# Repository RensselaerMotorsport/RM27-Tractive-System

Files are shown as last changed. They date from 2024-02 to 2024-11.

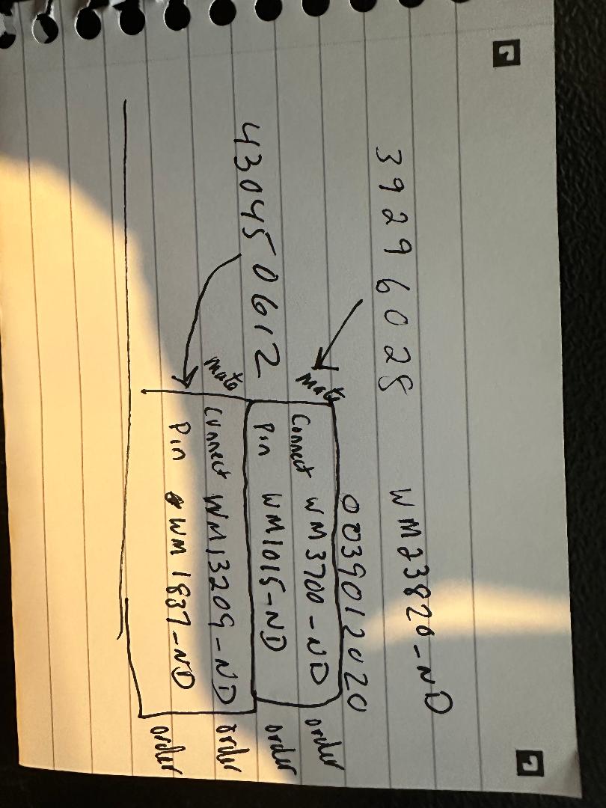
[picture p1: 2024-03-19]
mating connectors TSAL.jpg

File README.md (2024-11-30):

# RM27-TRACTIVE-SYSTEM

NOTICE!!!
This repo is OUTDATED! The current tractive system repository is at https://github.com/RensselaerMotorsport/RM28-Tractive-System
Almost all circuits from this repo were updated for the RM28 car (FSAE 2024 competition car)

This respository currently contains one major project:
* WIP RM27 Project - This project is the most up-to-date version of the 2023-2024 competition car's High Voltage System.

To open and work with these files, specific software packages must be used.
* LTSpice - Circuit simulation software used for preliminary mockups of circuit designs. The .asc files can be opened in other spice programs like ngspice or pspice, but these circuits were originally drafted in LTSpice
* KiCad - PCB design software used for creating schematics for manufacturing.

Acronyms Used:
* ESF - Elecrtrical Systems Form
* GLV - Grounded Low Voltage
* HV - High Voltage
* TSAL - Tractive System Active Light

Typical Circuits:
* Tractive System Active Light (TSAL) - When GLV is on and HV (typically between 12-400V) is less than 60V outside the container, turns an LED green. If HV is greater than 60V, a red LED blinks at low frequency. PS16-051 is the transformer used in this circuit, but has been since discontinued. A similar transformer may need to be selected.
* Accumulator Indicator - Turns on blue LED if voltage outside the container is greater than 60V. Must work in absence of GLV.
* ESF - Shows overall design of racecar electrical system. Includes datasheets, circuit diagrams, electrical architecture, and part numbers.

Additional Circuits in this repo:
The soldering demo board for the Mercer XLab was included to be used as an instructional tool to teach other students at RPI how to solder. Several PCBs were printed and the Rensselaer Motorsport club ran a soldering workshop in the XLab. The board is a simple multivibrator that uses a potentiometer to adjust the blinking frequency of an LED. This workshop was quite successful for our lab, however keep in mind if you run a workshop with this circuit, we designed this circuit to be used with a 3V button cell battery (CR2025). Make sure that a 555 timer designed to have a 3V power rail us used so the timer works sufficiently. (We used the TLC555CP).

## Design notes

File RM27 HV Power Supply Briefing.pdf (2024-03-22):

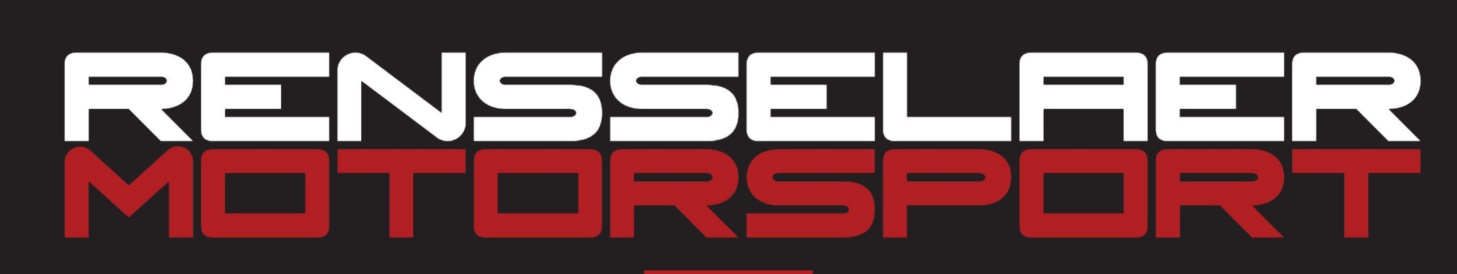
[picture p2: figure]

## RM27 HV Power Supply Briefing

Sean Trimper - ESO
trimps@rpi.edu - (603)204-0353 March, 2024

### - Use fancy HVPS without injury

## Goal

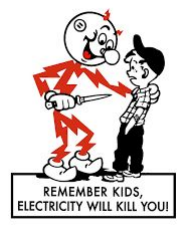
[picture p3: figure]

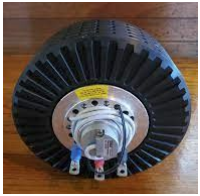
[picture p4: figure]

- In addition to being connected to 400V, the motor is heavy and

moving (and EXPENSIVE)

- The entire motor casing spins FAST
- Even if the motor has stopped moving:
- Ensure power is cut off from the tractive system
- Motor will be hot
- The ESC handles many volts and amps

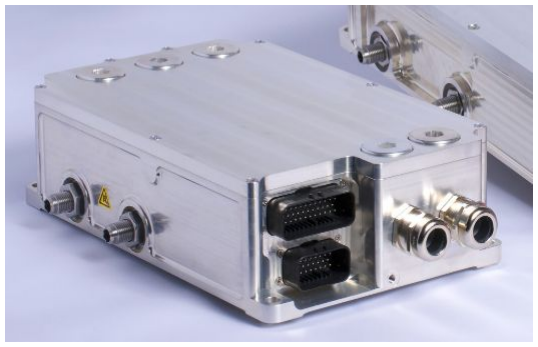
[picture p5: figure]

- ESC will be hot
- If handling motor or ESC, contact ESO

## Powertrain

## HVPS

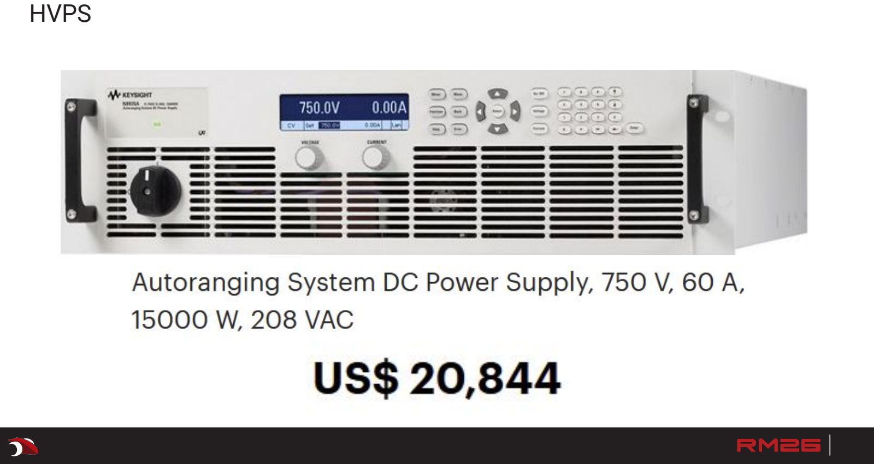
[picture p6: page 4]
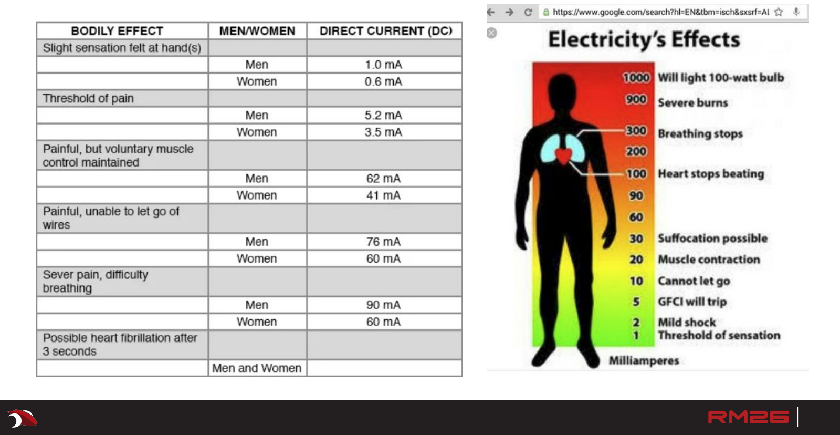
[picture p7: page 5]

- >50V = dead
- Do not touch the HVPS unless Sean tells you to
- Do not approach the setup when HVPS is on unless told to

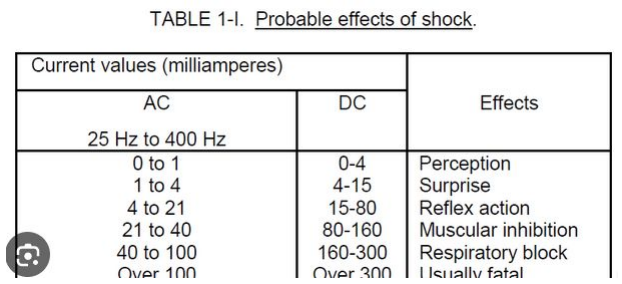
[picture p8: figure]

- Will announce verbally when HV work is being conducted and when it is over
- Treat the person with HV equipment on like they are actively welding
- If you touch it, you will have 1.5A (1500mA) across your heart at HV
- If you touch it, you will not be able to move, and will be “glued” to it (15mA)
- Electrical beating stick!
- Touch recently energized things with back of your hand (inverter, etc.)
- Keep one hand in your back pocket if not wearing HV gloves near HVPS

## High voltage

- Please familiarize yourself with the Shop Safety Manual
- Has EHS & faculty advisor approved guidelines on electrical work and safety
- If any questions arise while working, please ask in-person or on slack

## Questions?

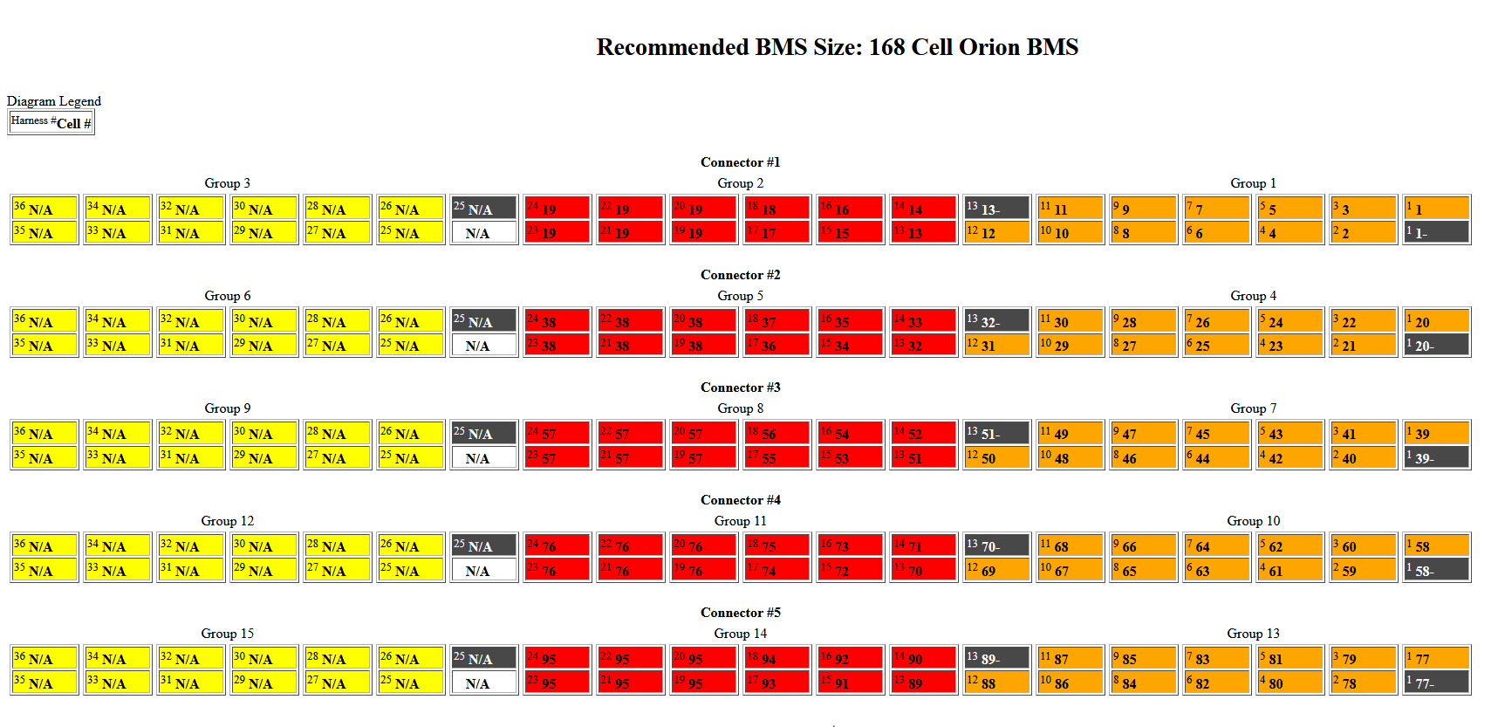
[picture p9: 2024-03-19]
BMS2-Voltage-Tap-Diagram.png

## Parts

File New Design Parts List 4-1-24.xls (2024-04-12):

Item | Qty | Reference | Part Description | Manufacturer / Part #
1 | 1 | C2 | CAP., 3.3uF, ALUM,450V,20% | NICHICON, ULT2W3R3MNL1GS | 493-6729-1-ND
2 | 1 | C3 | CAP., 10uF, X5R, 25V, 20%, 0603 | MURATA, GRM188R61E106MA73D | 490-7202-1-ND
3 | 1 | C8 | CAP., 10uF, X7R, 25V, 10%, 1206 | MURATA, GRM31CR71E106KA12L | 490-6518-1-ND
4 | 1 | C4 | CAP., 10pF, C0G, 630V,5%, 1206 | MURATA, GRM31A5C2J100JW01D | 490-11620-1-ND
5 | 1 | C5 | CAP., 0.33uF, X5R, 25V,10%, 0603 | AVX, 06033D334KAT2A | 478-KGM15BR51E334KTCT-ND
6 | 2 | C11,C12 | CAP., 22uF,X7R, 16V, 10%, 1210 | MURATA , GRM32ER71C226KE18L | 490-5313-1-ND
7 | 1 | C14 | CAP., 0.47uF, X7T, 450V, 10%, 1812 | TDK, C4532X7T2W474K230KA | 445-7771-1-ND
8 | 1 | C16 | CAP., 0.1uF, X7R, 25V, 10%, 0603 | MURATA, GRM188R71E104KA01D | 490-6051-1-ND
9 | 2 | D2,D3 | DIODE, RECTIFIER 600V, 1A, SOD123F | FAIRCHILD, ES1JFL | 1801-ES1JFLCT-ND
10 | 1 | D4 | DIODE SCHOTTKY, 30V, 200MA, SOD323 | CENTRAL SEMI., CMDSH2-3 TR | 1514-CMDSH2-3TRPBFREECT-ND
11 | 2 | D1, D5 | DIODE, ZENER, 5W,DO-214AA | MCC, SMBJ5350B-TP | SMBJ5350B-TPMSCT-ND
12 | 1 | N/A
13 | 1 | JP1 | Molex | 39296028 | WM23820-ND
14 | 1 | JP1 Mate | Molex | 39012025 | WM23700-ND
15 | 3 | JP1 Mate pin | Molex | 39000038 | WM2501CT-ND - Cut Tape (CT)
16 | 1 | JP2 | Molex | 532650229 | 0532650229-ND
17 | 1 | JP2 Mate | Molex | 510670200 | WM3330-ND
18 | 3 | JP2 Mate Pin | Molex | 502178000 | WM3316CT-ND
19 | 1 | L1 | INDUCTOR, 1500uH Wurth | 7447709152 | 732-4122-1-ND
20 | 1 | R3 | RES., CHIP, 4.99K, 1/4W, 1%, 1206 | VISHAY, CRCW12064K99FKEA | 541-4.99KFCT-ND
21 | 1 | R6 | RES., CHIP, 22.1k, 1/10W , 1%, 0603 | VISHAY, CRCW060322K1FKEA | 541-22.1KHCT-ND
22 | 1 | R9 | RES., CHIP, 10.7K, 1/10W, 1%, 0603 | VISHAY, CRCW060310K7FKEA | 541-10.7KHCT-ND
23 | 1 | R10 | RES., CHIP, 1.24K,1/10W, 1%, 0603 | VISHAY, CRCW06031K24FKEA | 541-1.24KHCT-ND
24 | 1 | R12 | RES., CHIP, 0.33 OHM, 0.2W, 1%, 0603 | RCWE0603R330FKEA | RCWE.33CCT-ND
25 | 1 | U1 | I.C., LT8315EFE | LINEAR, LT8315EFE#PBF | 505-LT8315EFE#PBF-ND
26 | 4 | MH1-MH4 | STANDOFF, NYLON, 0.25" | KEYSTONE, 8831 (SNAP ON) | 36-8831-ND
27 | 4 | R1,R2,R4,R5 | RES., CHIP, 249K, 1/4W, 1%, 1210 |  | 541-249KAACT-ND
28 | 1 | R7 | RES., CHIP, 20K, 1/4W, 1%, 1210 |  | 541-20.0KAACT-ND
29 | 1 | R8 | RES., CHIP, 1K, 1/4W, 1%, 1210 |  | 541-1.00KAACT-ND
30 | 2 | R100,R101 | RES., CHIP, 0, 1/10W, 1%, 0603 |  | 541-0.0GCT-ND
 |  |  | Bom changes on 8/3/17,9/5/17
5 | 1 | C5 | CAP., 0.33uF, X7R, 25V,10%, 0603 | TDK, C1608X7R1E334K080AC | 0 |  | 0 | Req,4/11/17
9 | 1 | D2 | DIODE, 600V, 1A, SOD123F | CENTRAL SEMI., CMMMR1U-06 TR | 0 | 500 | 500
9 | 1 | D3 | DIODE, SCHOTTKY 600V, 1.7A, 10PQFN | CREE, C3D1P7060Q | 0 |  | 0 |  | Lead Lime 18 weeks
18 | 1 | R9 | RES., CHIP, 5.36K, 1/10W, 1%, 0603 | VISHAY, CRCW06035K36FKEA | 0 |  | 0 | fr.1317A
19 | 1 | R10 | RES., CHIP, 619,1/10W, 1%, 0603 | VISHAY, CRCW0603619RFKEA | 0 | 2800 | 2800

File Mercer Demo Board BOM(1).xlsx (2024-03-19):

Part | Value | price/1 | link | Manufacturer P/N | Vendor Number | Vendor
U1 | 555 timer | 0.94 | https://www.digikey.com/en/products/detail/texas-instruments/TLC555CP/277502 | TLC555CP | 296-1857-5-ND | Digikey
J1 | N/A | 0.58 | https://www.amazon.com/LAMPVPATH-CR2032-Battery-Holder-Mounting/dp/B08SQJJJNK?s=electronics |  | B08SQJJJNK | Amazon
Button Cell | 3V | 0.4 | Button Cell (https://www.amazon.com/Powerowl-Capacity-Lithium-Battery-20-Pack/dp/B08ML4X69J?s=electronics) |  | B08ML4X69J
R2 | 1kohm | 0.1 | https://www.digikey.com/en/products/detail/stackpole-electronics-inc/CF14JT1K00/1741314 | CF14JT1K00 | CF14JT1K00CT-ND - Cut Tape (CT) | DIgikey
D1 | 1.9V | 0.28 | https://www.digikey.com/en/products/detail/sunled/XLUR12D/4745846 | XLUR12D | 1497-1031-ND | Digikey
Rpot |  | 1.2 | https://www.digikey.com/en/products/detail/tt-electronics-bi/P090S-14T20BR10K/2408854 | P090S-14T20BR10K | 987-1277-ND | Digikey
C1 | 10uF | 0.1 | https://www.digikey.com/en/products/detail/yageo/CC0805KRX7R9BB104/302874 | CC0805KRX7R9BB104 | 311-1140-1-ND - Cut Tape (CT) | Digikey
S1 | N/A | 1.5 | https://www.digikey.com/en/products/detail/cw-industries/GF-123-0054/4089770 | GF-123-0054 | CWI333-ND | Digikey
R1 | 150ohms | 0.1 | https://www.digikey.com/en/products/detail/stackpole-electronics-inc/RNF14FTD150R/1706642 | RNF14FTD150R | RNF14FTD150RCT-ND - Cut Tape (CT) | Digikey

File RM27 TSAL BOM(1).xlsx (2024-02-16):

Part | Value | Description | MFG Part Number | price/1 | price per accu | link | Total price | Vendor Number | Vendor
R6,R7,R4,R2 | 249kohm | R_1206_3216Metric_Pad1.42x1.75mm_HandSolder | RCV1206249KFKEA | 0.3 | 1.2 | https://www.mouser.com/ProductDetail/Vishay-Draloric/RCV1206249KFKEA?qs=hWgE7mdIu5TjDQ%252B0bO60Fg%3D%3D | 22.02 | 71-RCV1206249KFKEA | Mouser
J2 | Connector | Molex_Mini-Fit_Jr_5566-02A_2x01_P4.20mm_Vertical | 39296028 | 1.28 | 1.28 | https://www.digikey.com/en/products/detail/molex/0039296028/930308 |  | WM23820-ND | Digikey
R10, R11 | 100ohm | R_1206_3216Metric_Pad1.42x1.75mm_HandSolder | CRCW1206100RFKEAHP | 0.23 | 0.46 | https://www.digikey.com/en/products/detail/vishay-dale/CRCW1206100RFKEAHP/2222416 |  | 541-100UCT-ND - Cut Tape (CT) | Digikey
R12 | 1Mohm | R_1206_3216Metric_Pad1.42x1.75mm_HandSolder | CRCW12061M00FKEAC | 0.1 | 0.1 | https://www.digikey.com/en/products/detail/vishay-dale/CRCW12061M00FKEAC/7928596 |  | 541-4174-1-ND - Cut Tape (CT) | Digikey
C3,C4,C5 | 100nF | C_0805_2012Metric_Pad1.15x1.40mm_HandSolder | C0805C104K4RAC7800 | 0.19 | 0.57 | https://www.digikey.com/en/products/detail/kemet/C0805C104K4RAC7800/411166 |  | 399-C0805C104K4RAC7800CT-ND - Cut Tape (CT | Digikey
C2 | 10nF | C_0805_2012Metric_Pad1.15x1.40mm_HandSolder | C0805C104K4RAC7800 | 0.13 | 0.13 | https://www.digikey.com/en/products/detail/kemet/C0805C103K3RAC7800/2209705 |  | 399-C0805C103K3RAC7800CT-ND - Cut Tape (CT) | Digikey
R5 | 900ohm | R_1206_3216Metric_Pad1.42x1.75mm_HandSolder | RT1206CRE07900RL | 0.23 | 0.23 | https://www.digikey.com/en/products/detail/yageo/RT1206CRE07900RL/5938251 |  | 13-RT1206CRE07900RLCT-ND - Cut Tape (CT) | Digikey
R8 | 49k9 | R_1206_3216Metric_Pad1.42x1.75mm_HandSolder | ERJ-P08D4992V | 0.28 | 0.28 | https://www.digikey.com/en/products/detail/panasonic-electronic-components/ERJ-P08D4992V/9812440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 |  | 10-ERJ-P08D4992VCT-ND - Cut Tape (CT | Digikey
R9,R19,R13 | 2k2 | R_1206_3216Metric_Pad1.42x1.75mm_HandSolder | ERJ-P08F2201V | 0.21 | 0.63 | https://www.digikey.com/en/products/detail/panasonic-electronic-components/erj-p08f2201v/9812790 |  | 10-ERJ-P08F2201VCT-ND - Cut Tape (CT) | Digikey
D2 | 12V | D_DO-35_SOD27_P7.62mm_Horizontal | 1N5242BTR | 0.16 | 0.16 | https://www.digikey.com/en/products/detail/onsemi/1N5242BTR/977598 |  | 1N5242BFSCT-ND - Cut Tape (CT) | Digikey
R3 | 24kohm | R_1206_3216Metric_Pad1.42x1.75mm_HandSolder | CRCW120624K0FKEAC | 0.1 | 0.1 | https://www.digikey.com/en/products/detail/vishay-dale/CRCW120624K0FKEAC/7920772 |  | 541-CRCW120624K0FKEACCT-ND - Cut Tape (CT) | Digikey
Q3,Q1 | 2N7002 | SOT-23 | 2N7002 | 0.45 | 0.9 | https://www.digikey.com/en/products/detail/onsemi/2N7002/244345 |  | 2N7002NCT-ND - Cut Tape (CT) | Digikey
R18,R14 | 10k | R_1206_3216Metric_Pad1.42x1.75mm_HandSolder | CRCW120610K0FKEBC | 0.1 | 0.2 | https://www.digikey.com/en/products/detail/vishay-dale/CRCW120610K0FKEBC/7921127 |  | 541-CRCW120610K0FKEBCCT-ND - Cut Tape (CT) | Digikey
D1 | D | D_SMA | US1MDFQ-13 | 0.44 | 0.44 | https://www.digikey.com/en/products/detail/diodes-incorporated/US1MDFQ-13/6187532 |  | US1MDFQ-13DICT-ND - Cut Tape (CT) | Digikey
Q4,Q2 | MCT06P10-TP | SOT-223-3_TabPin2 | MCT06P10-TP | 0.77 | 1.54 | https://www.digikey.com/en/products/detail/micro-commercial-co/MCT06P10-TP/10054657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 |  | MCT06P10-TPMSCT-ND - Cut Tape (CT) | Digikey
J1 | Connector | Molex_Micro-Fit_3.0_43045-0612_2x03_P3.00mm_Vertical | 430450612 | 1.52 | 1.52 | https://www.digikey.com/en/products/detail/molex/0430450612/252504?s=N4IgTCBcDaICwGYAMcCsBaJA2AjBAugL5A |  | WM1791-ND | Digikey
U2 | LM311 | SOIC-8_3.9x4.9mm_P1.27mm | LM311DR | 0.42 | 0.42 | https://www.digikey.com/en/products/detail/texas-instruments/LM311DR/381217 |  | 296-1388-1-ND - Cut Tape (CT) | Digikey
R17 | 220kohm | R_1206_3216Metric_Pad1.42x1.75mm_HandSolder | CRCW1206220KFKEAHP | 0.23 | 0.23 | https://www.digikey.com/en/products/detail/vishay-dale/CRCW1206220KFKEAHP/2228003 |  | 541-220KUCT-ND - Cut Tape (CT) | Digikey
R15,R16 | 22kohm | R_1206_3216Metric_Pad1.42x1.75mm_HandSolder | CRCW120622K0FKEA | 0.1 | 0.2 | https://www.digikey.com/en/products/detail/vishay-dale/CRCW120622K0FKEA/1176794 |  | 541-22.0KFCT-ND - Cut Tape (CT) | Digikey
U4 | NE555 | SOIC-8_3.9x4.9mm_P1.27mm | NE555DR | 0.47 | 0.47 | https://www.digikey.com/en/products/detail/texas-instruments/NE555DR/372491 |  | 296-6501-1-ND - Cut Tape (CT) | Digikey
U3 | 4N35 | DIP-6_W7.62mm | 4N35 | 0.74 | 0.74 | https://www.digikey.com/en/products/detail/vishay-semiconductor-opto-division/4N35/1738522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 |  | 4N35-ND | Digikey
C6,C1 | 1uF | C_0805_2012Metric_Pad1.15x1.40mm_HandSolde | C0805C105K4RACAUTO | 0.17 | 0.34 | https://www.digikey.com/en/products/detail/kemet/C0805C105K4RACAUTO/3314924 |  | 399-6930-1-ND - Cut Tape (CT) | Digikey
D3 | VHI | LED_0805_2012Metric_Pad1.15x1.40mm_HandSolder | CMD17-21VRD/TR8 | 0.76 | 0.76 | https://www.digikey.com/en/products/detail/visual-communications-company-vcc/CMD17-21VRD-TR8/254853 |  | L62501CT-ND - Cut Tape (CT) | Digikey
U1 | SPAN02A-12 | SPAN02 | SPAN02A-12 | 8.74 | 8.74 | https://www.mouser.com/ProductDetail/MEAN-WELL/SPAN02A-12?qs=5aG0NVq1C4wxQqKsG84AkQ%3D%3D |  | 709-SPAN02A-12 | Mouser
R1 | 75kohm | R_1206_3216Metric_Pad1.42x1.75mm_HandSolder | CRCW120675K0FKEAHP | 0.38 | 0.38 | https://www.digikey.com/en/products/detail/vishay-dale/CRCW120675K0FKEAHP/2227954 |  | 541-CRCW120675K0FKEAHPCT-ND - Cut Tape (CT) | Digikey

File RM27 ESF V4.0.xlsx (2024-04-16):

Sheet: Overview
Instructions |  |  | Status
-All cells for input have an orange background. -Cells, sections and worksheets have an overall status. The status cells have a blue background. -For sections which require an image or schematic, the image should be pasted and located over the specified area. Images should be pasted at a high resolution and then resized. This allows the reader to zoom into the image if more resolution is required. -Where datasheets are requested, a hyperlink to the datasheet from the manufacturer must be provided. -Additional Comments sections are provided throughout for documentation of things which the team feels are not adequately documented in the provided fields. These are optional and do not need to be completed. |  |  | Datasheets | OK
 |  |  | TS Schematics | OK
 |  |  | Accumulator | OK
 |  |  | Precharge/Discharge | OK
 |  |  | Charging | OK
 |  |  | Shutdown Circuit | OK
 |  |  | Torque Security | OK
 |  |  | Other | OK
 |  |  | Team Name | Rensselaer Motorsport
 |  |  | University | Rensselaer Polytechnic Institute
 |  |  | Competition Year | 2024
 |  |  | Max TS Voltage | 399 | V
 |  |  | Accumulator Fuse | 90 | A
Additional Comments
Template Revision History
Version | Date | Comment
2.3 | 2023-10-29 | Updated for 2024 season.
2.2 | 2022-11-03 | Updated for 2023 season.
2.1 | 2021-10-22 | Updated for 2022 season.
2.0 | 2020-11-27 | Multiple updates and bug fixes.

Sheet: Datasheets
Status | OK
Battery Cell |  |  |  | OK
Make |  | Molicel
Model |  | P28A
Nominal Capacity |  | 2.8 | Ahr
Maximum Voltage |  | 4.2 | V
Nominal Voltage |  | 3.6 | V
Minimum Voltage |  | 2.5 | V
Max output current |  | 35 | A
Max continuous current |  | 25 | A
Max Cell temp |  | 60 | C
Cell Chemistry |  | LiNiMnCoO2 (NMC)
Datasheet |  | https://www.molicel.com/wp-content/uploads/INR18650P28A-V1-80093.pdf
SDS |  | https://www.molicel.com/wp-content/uploads/00058ar-Molicel-SDS-Y2020.pdf
Additional Comments
Conductors |  |  |  |  |  |  |  |  | OK
Manufacturer | Part Number | Size [mm2] | Voltage [V] | Ampacity [A] | Max Temp [C] | Datasheet |  | Location Used |  | Additional Comments |  |  |  |  | Rules References
Champlain Cable EXRAD | EXRAD® ERGOFLEX ISO 19642-9 EXRAD–EF/EF-TW-50 | 50 | 1000 | 160 | 150 | https://www.champcable.com/wp-content/uploads/2021/06/219.-EXRAD-ERGOFLEX-Shielded-Thin-Wall-Battery-Cable-R3.pdf |  | Internal accumulator components, inverter to motor | OK | Listed Ampacity is at maximum allowed conductor temperature of 150C. At 90C, it is 260 Amps. Shielded |  |  |  |  | EV.5.2.1 EV.5.2.5 EV.6.3 EV.6.3.2 EV.6.6.4
Team Built | Busbar Collector | 79.6 | N/A | 154 | 90 | N/A |  | Accumulator Segment Poles | OK | Copper collectors
Team Built | Busbar | 2.5 | N/A | 9.7 | 90 | N/A |  | Accumulator segments (negative side of cells) | OK | Parallel nickel bus bars
Super Vu-Tron | 01764 | 55 | 600 | 260 | 90 | https://www.awcwire.com/product/01764 |  | Accumulator to inverter (including energy meter, HVD) | OK | Additional high current wire (unshielded)
AWC | M22759/22-22 | 0.34 | 600 | 0.92 | 200 | https://www.awcwire.com/product/m22759_22-22 |  | IMD, Precharge, Discharge | OK | HV to IMD and pre/discharge wiring
KOLACEN | ‎KLFH-027 | 1.31 | 250 | 15 | N/A | https://www.ubuy.com.bh/en/product/40R2G2HDU-kolacen-automotive-car-inline-screw-type-6x30mm-agc-fuse-holder-16-awg-wire-pcak-of-10 |  | AMS Fuse Holder | OK | Fuse holder from voltage tap to BMS
Fuses |  |  |  |  |  |  |  |  | OK
Manufacturer | Part Number | Voltage [V] | AC/DC | Current [A] | Interrupt [A] | Datasheet |  | Location Used |  | Additional Comments |  |  |  |  | Rules References
Bojack | F2AL250V | 250 | DC | 2 | 1000 | AMS Fuse (https://www.amazon.com/BOJACK-5x20mm-F2AL250V-Fast-Blow-Glass/dp/B07S768TPM) |  | AMS voltage sense | OK |  |  |  |  |  | EV.5.2.1 EV.6.6
Littelfuse | L50QS090.T | 500 | DC | 90 | 50000 | Main Fuse (https://www.mouser.com/datasheet/2/240/L50QS_High_Speed_Fuse_Datasheet-3311429.pdf) |  | Main Fuse | OK
Bel Fuse | 0ADKC5000-BE | 500 | DC | 5 | 20000 | Energy Meter Fuse (https://www.mouser.com/datasheet/2/643/ds_cp_0adkx_series-1960352.pdf) |  | Energy Meter Fuse | OK
Schurter Inc. | 8020.5071.G | 400 | DC | 2 | 1500 | IMD Fuse (https://www.schurter.com/en/datasheet/typ_SHF_6.3x32.pdf) |  | IMD | OK | HV to IMD (needed due to wires >= 150mm)
Resistors |  |  |  |  |  |  |  |  |  |  |  | OK
Manufacturer | Part Number | Voltage [V] | Resistance [Ω] | Power [W] | Power for 15 sec [W] | Heatsink [°C/W] (Enter "None" if no heatsink) |  |  | Datasheet |  | Location Used |  | Additional Comments |  |  |  | Rules References
Caddock Electronics Inc. | MP925-10.0K-1% | 500 | 10,000 | 25 | N/A | None |  |  | MP925 (https://www.mouser.com/datasheet/2/62/MP9000_Series-1052.pdf) |  | TSMP | OK |  |  |  |  | EV.5.2.1 EV.5.6 EV.5.8.4
Ohmite | 850F750E | 1170 | 750 | 50 | 750 | 3 |  |  | 850F750E (https://www.ohmite.com/assets/docs/res_89.pdf?r=false) |  | Precharge/Discharge | OK | Manufacturer tests at 5x rated power for 5sec. 250W>212W peak. 50W>46W avg.
Contactors/Relays |  |  |  |  |  |  |  |  | OK
Manufacturer | Part Number | Voltage [V] | Continuous Current [A] | Max Interrupt Current [A] | Normal State | Datasheet |  | Location Used |  | Additional Comments |  |  |  |  | Rules References
TE Connectivity / Kilovac | LEV200A4NAA | 900 | 500 | 2000 | NO | LEV200A4NAA (https://www.mouser.com/datasheet/2/418/ENG_CS_5-1773450-5_sec7_LEV200_0313_5-1773450-5_Se-1074401.pdf) |  | AIR | OK |  |  |  |  |  | EV.5.2.1 EV.5.4 EV.5.6
Cynergy3 | DBT71205F-HR | 3500 | 3 | 2 | NC | DBT71205F-HR (https://www.mouser.com/datasheet/2/657/cynergy3_d_hr_v2-1892317.pdf) |  | Discharge | OK
Cynergy3 | DAT71205F-HR | 3500 | 3 | 2 | NO | DAT71205F-HR (https://www.mouser.com/datasheet/2/657/cynergy3_d_hr_v2-1892317.pdf) |  | Precharge | OK
Connectors |  |  |  |  |  |  |  | OK
Manufacturer | Part Number | Voltage [V] | Ampacity [A] | Wire Size [mm2] | Datasheet |  | Location Used |  | Additional Comments |  |  |  |  | Rules References
Amphenol | MSDM5002 | 1000 | 500 | 50 | HVD Plug (https://www.mouser.com/datasheet/2/18/1/msd_m_xxxx_rev_a_cdr-1853453.pdf) |  | HVD | OK | HVD, Plug |  |  |  |  | EV.5.2.1 EV.5.10 EV.6.3.3
Amphenol | MSDF000R | 1000 | 500 | 50 | HVD Receptacle (https://www.mouser.com/datasheet/2/18/Amphenol_08092019_MSDF000R-1626989.pdf) |  | HVD | OK | HVD, Receptacle. HVD is main conductor connector for current to controller
Amphenol | RL0-080-1-50 | 1000 | 200 | 50 | RLO-080-1-50 (https://www.mouser.com/datasheet/2/18/1/IDS_67_RADLOK-372465.pdf) |  | Accumulator Segments | OK | Maintenance Plug, Connector
Amphenol | RL9080-101 | 1000 | 200 | 50 | RL9080-101 (https://www.mouser.com/datasheet/2/18/1/IDS_67_RADLOK-372465.pdf) |  | Accumulator Segments | OK | Maintenance Plug, Pin
Littelfuse | 576-03450613H | 600 | 20 | N/A | E-Meter Fuse Holder (https://www.mouser.com/datasheet/2/240/media-3319810.pdf) |  | Energy meter fuse holder | OK | Soldered terminals, low current fuse
Amphenol | PL28V-301-50 | 1000 | 300 | 70 | Exit Plug (https://www.mouser.com/datasheet/2/18/1/c_powerlok_right_angle_plugs_1_2_3_way_cdr-1701769.pdf) |  | Outer wall of accumulator container, charger output to accumulator | OK | Exterior Container Plug
Amphenol | PL00V-301-10M8 | 1000 | 300 | 70 | Exit Pin (https://www.amphenol-industrial.de/media/pages/produkte/ev-steckverbinder/powerlok/geratestecker-1-polig-pl00v30110m8/98e87c60fe-1710336547/cdr-u-plm-daten-we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) |  | Maintenance plug/Inner wall of accumulator container | OK | Exterior Container Pin / Additonal MT plug pin
Amphenol | SLPIPB70BSO2EH | 1000 | 250 | 70 | SLPIPB70BSO2EH (https://www.mouser.com/datasheet/2/18/C10-738727_CUS_A-1316208.pdf) |  | Accumulator Segments | OK | Maintenance Plug, Connector (additional)
Amphenol | HVSL633063A106I | 800 | 40 | 16 | AC In (https://www.amphenol-industrial.de/en/amph/download/getMime/Yy1odnNsNjMzMDYzeHh4eGktcmV2LWMtY2RyLnBkZg==) |  | Charger Input | OK | AC in to charger
Pomona Electronics | 72930 | 1000 | 36 | N/A | TSMP (https://www.pomonaelectronics.com/file/18219/download?token=QVAf-7MO) |  | TSMP - start panel | OK | TSMP connector. One red, one black, same part electrically
Molex | 192210241 | N/A | 230 | 55 | TS Ring Terminals (https://www.molex.com/en-us/products/part-detail/192210241?display=pdf) |  | Energy meter, Motor, HVD, Main fuse, AIRs | OK | Ring terminals crimped onto main TS cable. Used in various locations when attaching to bolted connection (HVD, energy meter, motor phases, main fuse, AIRs)
Amphenol | RL9080-301-F1 | 1000 | 200 | 50 | RL9080-301-F1 (https://www.mouser.com/datasheet/2/18/1/IDS_67_RADLOK-372465.pdf) |  | Accumulator Divider Wall | OK | Maintenance Plug, pin to pin, on divider wall
Insulating Materials |  |  |  |  |  |  |  |  |  | OK
Manufacturer | Part Number | Thickness [mm] | Dielectric strength [V/mm] | Voltage Rating [V] | Max Temp [C] | Flammability Rating | Datasheet |  | Location Used |  | Additional Comments |  |  |  |  | Rules References
McMaster-Carr | 85345K651 | 62.5 | 350 | 21875 | 137.778 | UL 94 V-0 | https://www.mcmaster.com/85345K651/ |  | Accumulator | OK | Used in between segments to insulate segments from accumulator container walls |  |  |  |  | EV.5.2.1 EV.5.2.2.a EV.5.2.3 EV.5.4.4 EV.6.2 EV.6.5.5.a
MG Chemicals | 4223F-55ML | 2 | 1000 | 2000 | 125 | N/A | https://mgchemicals.com/downloads/tds/tds-4223f-l.pdf |  | TSAL PCB | OK | UV-A flourescent
MYJOR | Kapton | 1 | 4500 | 4500 | 350 | N/A | https://www.amazon.com/Temperature-Kapton-Professional-Protecting-Circuit/dp/B08NY4914D |  | Segments, accumulator container edges, motor connections | OK | Used to fill gaps between line 95 insulation, on top of cell segments (covering connections) and near motor HV connections.

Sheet: TS Schematics
Status | OK
Tractive System Schematic |  |  |  |  | Accumulator TS Schematic |  |  |  | Additional Comments
 |  |  |  |  |  |  |  |  | Voltage indicator below. EN (enable) = 1.22V through voltage divider when "400V" = 60V. If EN pin on LT8315 >1.22V, output is enabled. Thus, as the input voltage exceeds 60V on its way to max TS voltage, the output is enabled and the light turns on.
Vehicle Tractive System Schematic Shows |  |  |  | OK | Accumulator TS Schematic Shows |  |  | OK | Connectors between HVD, Energy Meter, and motor are ring connectors. Connections in and out of motor controller are built in to the controller. Set screw used to restrain cable into inverter. Energy meter is housed in a 3D printed housing.
Rules References |  |  |  |  | Rules References
 |  | Shows details of all TS circuits outside of accumulator | TRUE | OK |  | Details of all TS circuits within accumulator | TRUE | OK
 |  | Accumulator is shown as a single element (without internal details) | TRUE | OK |  | All wire gauges labeled | TRUE | OK
 |  | All wire gauges labeled | TRUE | OK |  | All fuses labeled with ampacity | TRUE | OK
 |  | All fuses labeled with ampacity | TRUE | OK | EV.6.6.6 | All wires > 150mm have a fuse within the first 150mm from the source | TRUE | OK
EV.6.6.6 |  | All wires > 150mm have a fuse within the first 150mm from the source | TRUE | OK |  | Fuse locations represent physical location | TRUE | OK
 |  | Fuse locations represent physical location | TRUE | OK |  | Connectors labeled with Make/Model | TRUE | OK
 |  | Enclosures shown | TRUE | OK |  | Standard schematic symbols used | TRUE | OK
 |  | Connectors labeled with Make/Model | TRUE | OK |  | All text is readable (zooming is allowed) | TRUE | OK
 |  | Standard schematic symbols used | TRUE | OK | EV.5.4 | AIRs | TRUE | OK
 |  | All text is readable (zooming is allowed) | TRUE | OK | EV.5.3 | Maintenance plugs | TRUE | OK
EV.5.8 |  | TSMPs | TRUE | OK |  | Cells (details of all intercell connections may be abstracted) | TRUE | OK
 |  | Motor Controller | TRUE | OK | EV.5.7 | Accumulator Indicator | TRUE | OK
 |  | Motor | TRUE | OK
EV.5.8.5 |  | TSMPs not fused | TRUE | OK
Must be shown on at least one schematic |  |  |  | OK
Rules References
EV.7.6 |  | IMD | TRUE | OK
EV.5.5 |  | HVD | TRUE | OK
EV.5.6 |  | Precharge | TRUE | OK
EV.5.6 |  | Discharge | TRUE | OK
EV.3.2; EV.5.1.3 |  | Energy Meter | TRUE | OK
EV.5.6.1.c |  | Precharge is not fused | TRUE | OK
EV.5.6.1.c |  | Discharge is not fused | TRUE | OK

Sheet: Accumulator
Status | OK
Segment-to-Segment Connection |  |  |  | Series |  | OK
Maximum TS Voltage |  |  |  | 399 | V | OK
Nominal TS Voltage |  |  |  | 342 | V
Total Cells |  |  |  | 570
Segment Data |  |  |  |  |  |  |  |  | OK | BMS |  |  |  |  | OK | Maintenance Plugs |  |  |  | OK | Insulating Materials |  |  |  |  | OK | Additional Comments
Cell Connection Order |  |  | Parallel then Series |  |  |  |  |  | OK | BMS Type |  |  | Centralized |  | OK | Connector |  | Amphenol PL28V-301-50 |  | OK | Between cells and accum. container |  |  | McMaster-Carr 85345K651 |  | OK | No wires >150mm (no fuses for those wires needed). Using 2 types of Maintenance Plugs: one on the segments and one on the exterior of the container. Plug with the lower ampacity listed on this page, but both listed in datasheets page.
Segment | Parallel cells | Series cells | Temp Sensors | Accumulator Number | Max Voltage [V] |  | Segment Energy [MJ] |  |  | BMS Source |  |  | Purchased |  | OK | Ampacity |  | 300 | A | OK | Voltage Rating |  |  | 21875 | V | OK
 |  |  |  |  |  |  |  |  |  | Make | Orion | Model | BMS2 180-Cell |  | OK | Segment Fuse |  |  |  |  | Temperature Rating |  |  | 137.778 | C | OK
1 | 6 | 19 | 29 | 1 | 79.8 |  | 4.826304 |  | OK | Galvanic Isolation TS to GLV |  |  | 1500 | V | OK | Segment Fuse Ampacity |  | #N/A | A |  | Flammability Rating |  |  | UL 94 V-0
2 | 6 | 19 | 29 | 1 | 79.8 |  | 4.826304 |  | OK | Galvanic Isolation between segments |  |  | 2500 | V | OK | AIR |  |  |  |  | On top of cells |  |  | McMaster-Carr 85345K651 |  | OK
3 | 6 | 19 | 29 | 1 | 79.8 |  | 4.826304 |  | OK | Galvanic Isolation device |  |  |  |  |  | Make/Model |  | TE Connectivity / Kilovac LEV200A4NAA |  | OK | Voltage Rating |  |  | 21875 | V | OK
4 | 6 | 19 | 29 | 1 | 79.8 |  | 4.826304 |  | OK | Gavlanic Isolation device datasheet |  |  |  |  |  | Contact Voltage Rating |  | 900 | V | OK | Temperature Rating |  |  | 137.778 | C | OK
5 | 6 | 19 | 29 | 1 | 79.8 |  | 4.826304 |  | OK | Voltage Sense Leads |  |  |  |  |  | Max switching current |  | 2000 | A |  | Flammability Rating |  |  | UL 94 V-0
6 |  |  |  |  | 0 |  | 0 |  |  | Max Sense Lead Length |  |  | 90 | cm | OK | Max continuous current |  | 500 | A | OK | Separating AIR and Fuse from cells |  |  | McMaster-Carr 85345K651 |  | OK
7 |  |  |  |  | 0 |  | 0 |  |  | Sense Lead Overcurrent Protection Device |  |  | Bojack F2AL250V |  | OK | Main Fuse |  |  |  |  | Voltage Rating |  |  | 21875 | V | OK
8 |  |  |  |  | 0 |  | 0 |  |  | Overcurrent Location |  |  | Conductor |  | OK | Main Fuse |  | Littelfuse L50QS090.T |  | OK | Temperature Rating |  |  | 137.778 | C | OK
9 |  |  |  |  | 0 |  | 0 |  |  | Overcurrent Other Location |  |  |  |  |  | Main fuse ampacity |  | 90 | A |  | Flammability Rating |  |  | UL 94 V-0
10 |  |  |  |  | 0 |  | 0 |  |  | Overcurrent Voltage Rating |  |  | 250 |  | OK | Main fuse voltage |  | 500 | V | OK
11 |  |  |  |  | 0 |  | 0 |  |  | Temperature Sensors
12 |  |  |  |  | 0 |  | 0 |  |  | Temp Sensor Location |  |  | On bus bar |  | OK
13 |  |  |  |  | 0 |  | 0 |  |  | Distance to cell terminal |  |  | 4 | mm | OK
14 |  |  |  |  | 0 |  | 0 |  |  | Cells sensed per sensor |  |  | 1 | cells | OK
15 |  |  |  |  | 0 |  | 0 |  |  | Thermal Contact material used |  |  | Mcmaster 1272N15
16 |  |  |  |  | 0 |  | 0 |  |  | Thermal contact material datasheet |  |  | Silicon Rubber Sheet (https://www.mcmaster.com/1272N15/) |  | OK
17 |  |  |  |  | 0 |  | 0 |  |  | Thermal contact material conductivity |  |  | 5 | W/(m∙K) | OK
18 |  |  |  |  | 0 |  | 0 |  |  | Thermal contact material thickness |  |  | 0.5 | mm | OK
 |  |  |  |  |  |  |  |  |  | Percent of cells sensed |  |  | 25.43859649 | % | OK
 |  |  |  |  |  |  |  |  |  |  |  |  |  |  |  |  |  |  |  |  |  |  |  |  |  |  |  |  |  | Picture of Segment Insulation between Cell Terminals and Sides of Accumulator Container |  |  | Picture of Insulation on Top of Segment
Maintenance Plug(s) Picture Shows |  |  |  |  |  |  | OK |  | Cell Connections Picture Shows |  |  |  |  |  | OK |  | Temperature Sensor Picture Shows |  |  |  |  |  | OK | Fuse and AIR Separation Picture Shows |  |  |  |  | OK | Segment Insulation Picture Shows |  | OK | Segment Insulation Picture Shows |  | OK
Unique Configuration of plugs |  |  |  |  |  | TRUE | OK |  | Bolted connection have positive locking |  |  |  |  | TRUE | OK |  | Temp sensor in direct contact with terminal or busbar |  |  |  |  | TRUE | OK | Fuse and AIR are separated from cells |  |  |  | TRUE | OK | Insulation between cells and accumulator container | TRUE | OK | Insulation on top of cells (air not acceptable) | TRUE | OK
Non-conductive on un-necessary surface |  |  |  |  |  | TRUE | OK |  | location of parallel cell overcurrent for parallel cells |  |  |  |  | TRUE | OK |  | Distance from sensor to cell negative terminal |  |  |  |  | TRUE | OK | Additional Comments |  |  |  |  | Rules References | Additional Comments |  | Rules References | Additional Comments |  | Rules References
Accessible without any additional accumulator disassembly |  |  |  |  |  | TRUE | OK |  | Additional Comments |  |  |  |  |  | Rules References |  | Additional Comments |  |  |  |  |  | Rules References | Fuses and AIR seperated by dividing wall (shown in image in orange) which also has electrical insulation on the cell/segment side |  |  |  |  | EV.5.4.4 | Cross section view, green is insulation material |  | EV.5.2.2.a EV.5.2.3 | Insulation applied to bottom side of the lid, marked in green |  | EV.5.2.2.a EV.5.2.3
Positive Locking |  |  |  |  |  | TRUE | OK |  | The copper busbar sits directly on top of an additional nickel busbar spot-welded to battery cells The transparent layer covering the busbars is a polycarbonate cover riveted at each corner |  |  |  |  |  | EV.6.4.1 EV.6.4.3 |  | The nickel busbar across the negative terminals is hidden to show inter-cell distances |  |  |  |  |  | EV.7.5
Additional Comments |  |  |  |  |  |  | Rules References
Copper in brown, HV wire in orange Little to no slack in HV wire to prevent user from plugging into the incorrect receptacle Left photo is behind interval dividing wall, right photo is in front of internal dividing wall Copper busbars are heatshrunk |  |  |  |  |  |  | EV.5.3
Parallel Cell Fusing |  |  |  |  | OK | Rules Referenes
Source |  |  | Team Designed |  | OK | EV.6.6.3 EV.6.6.5
Make/Model
Continuous Current |  |  | #N/A | A
Continuous Current |  |  | 47 | A | #NAME?
Test Data Summary
Tests at current 1 |  |  | 4 |  | OK |  |  | 47
Tests at current 2 |  |  | 4 |  | OK |  | 0.1 | 47
Tests at current 3 |  |  | 4 |  | OK |  | 1000
Tests at current 4 |  |  | 4 |  | OK
See Fusible Link Testing Guideline on FSAEOnline.com
Testing | Current [A] | Time to blow [s]
Test 1 | 47.15 | 160
Test 2 | 47.15 | 266
Test 3 | 47.15 | 205
Test 4 | 47.15 | 221
Test 5 | 47.32 | 5.56
Test 6 | 47.33 | 10.2
Test 7 | 47.35 | 11.86
Test 8 | 48.59 | 13.97
Test 9 | 77.66 | 0.776
Test 10 | 77.58 | 0.784
Test 11 | 77.71 | 0.774
Test 12 | 77.52 | 0.76
Test 13 | 204.24 | 0.066
Test 14 | 204.31 | 0.07
Test 15 | 204.41 | 0.061
Test 16 | 209.72 | 0.06

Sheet: PrechargeDischarge
Status | OK
Precharge |  |  |  | OK | Discharge |  |  | OK | TSMP |  |  | OK | Rules References
Resistor |  | Ohmite 850F750E |  | OK | Resistor | Ohmite 850F750E |  | OK | Resistor | Caddock Electronics Inc. MP925-10.0K-1% |  | OK | EV.5.8.4
# parallel |  | 1 |  | OK | # parallel | 1 |  | OK | # parallel | 1 |  | OK
# series |  | 1 |  | OK | # series | 1 |  | OK | # series | 1 |  | OK
Resistance |  | 750 | Ohms |  | Resistance | 750 | Ohms |  | Resistance | 10000 | Ohms | OK
Cont power |  | 50 | W |  | Cont power | 50 | W |  | Cont power | 25 | W | OK
power @15 sec |  | 750 | W |  | power @15 sec | 750 | W | OK | Voltage | 500 | V | OK
Voltage |  | 1170 | V | OK | Voltage | 1170 | V | OK
Bus Capacitance |  | 0.44 | mF | OK | Peak power | 212.268 | W
End of precharge |  | Time |  | OK | Peak current | 0.53 | A
time |  | 3 | sec | OK | Discharge time (to 60V) | 0.625223562 | s | OK
delta V |  |  | V |  | Relay | Cynergy3 DBT71205F-HR |  | OK
ending ratio |  |  | % |  | Relay voltage rating | 3500 | V | OK
Peak power |  | 212.268 | W |  | Relay current rating | 3 | A | OK
Peak current |  | 0.53 | A |  | Normal State | NC |  | OK
time to 90% |  | 0.76 | sec |  | Rules References
Precharge Res Energy to 90% |  | 34.67 | J |  | EV.5.6; EV.7.2.2c
Average Power |  | 45.6 | W
Relay |  | Cynergy3 DAT71205F-HR |  | OK
Relay voltage rating |  | 3500 | V | OK
Relay current rating |  | 3 | A | OK
Additional Comments

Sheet: Charging
Status | OK
Charger |  |  |  |  | OK |  | Additional Comments
Make |  |  | Elcon |  | OK
Model |  |  | 6.6kW HK-J CAN UHF |  | OK
Datasheet |  |  | Elcon Charger |  | OK
Input Voltage |  |  | 85~265 | V | OK
Input Current |  |  | 32A | A | OK
Output Voltage |  |  | 170-650 | V | OK
Output Current |  |  | 12 | A | OK
Power |  |  | 6.6 | kW | OK
Input to Output isolation |  |  | 2000 VAC 10 mA |  | OK
Charging Tractive System Schematic
Charging Tractive System Schematic Shows |  |  |  |  |  |  | OK | Charging Shutdown Circuit Shows |  |  | OK
Rules References |  |  |  |  |  |  |  | Rules References
 |  | Fuse |  |  |  | TRUE | OK | EV.8.3 | IMD Control and Powerstage | TRUE | OK
 |  | Connectors |  |  |  | TRUE | OK | EV.8.3 | AMS | TRUE | OK
 |  | Wire Gauge |  |  |  | TRUE | OK | EV.8.2.7 | Charger Shutdown Button | TRUE | OK
EV.8.4 |  | IMD |  |  |  | TRUE | OK | EV.8.4 | AIRs | TRUE | OK
EV.8.4.2 |  | AIRs |  |  |  | TRUE | OK |  | Charge Connector Interlock | TRUE | OK
EV.8.2.6 |  | TSMPs |  |  |  | TRUE | OK |  | Charge Control (CAN, Enable, etc.) | TRUE | OK
Additional Comments |  |  |  |  |  |  |  | Additional Comments

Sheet: Shutdown Circuit
Status | OK
IMD |  |  |  |  | OK | BSPD |  |  |  | OK
Rules Reference |  |  | EV.7.6 |  |  | Rules Reference |  | EV.7.7
Make/Model |  |  | Bender iso175 |  | OK | Current Sensor Make/Model |  | DHAB S/124 |  | OK
Setpoint |  |  | 200 | kΩ | OK | Current Sensor Datasheet |  | Current Sensor |  | OK
 |  |  |  |  |  | Trip Current |  | 14.6 | A | OK
 |  |  |  |  |  | Sensor Output @ Trip Current |  | 2.89 | V | OK
 |  |  |  |  |  | Accuracy @ Trip Current |  | 0.4 | A | OK
Shutdown Circuit Schematic
Shutdown Circuit Schematic Shows |  |  |  |  |  |  |  | OK |  | BSPD System Schematic Shows |  | OK
Rules References
EV.7.9 |  | GLVMS |  |  |  |  | TRUE | OK |  | BSPD Current Sensor input open/short circuit protection | TRUE | OK
EV.7.9 |  | TSMS |  |  |  |  | TRUE | OK |  | BSPD Brake Position input open/short circuit protection | TRUE | OK
EV.7.10 |  | 2 Side Shutdown Buttons |  |  |  |  | TRUE | OK |  | Shutdown circuit powerstage | TRUE | OK
EV.7.10 |  | 1 Cockpit Shutdown Button |  |  |  |  | TRUE | OK |  | Additional Comments | Rules References
T.3.3 |  | Brake Over Travel Switch (BOTS) |  |  |  |  | TRUE | OK |  |  | EV.7.7
T.9.4 |  | Inertia Switch |  |  |  |  | TRUE | OK
EV.7.3 |  | AMS |  |  |  |  | TRUE | OK
EV.7.6 |  | IMD |  |  |  |  | TRUE | OK
EV.7.7 |  | BSPD |  |  |  |  | TRUE | OK
EV.5.5.2 |  | HVD Interlock |  |  |  |  | TRUE | OK |  | TSAL Schematic
EV.7.1.4 |  | IMD, AMS, BSPD have independent power stages |  |  |  |  | TRUE | OK
EV.4.1.3 |  | Outboard Wheel Motor Interlocks |  |  |  |  | TRUE | OK
 |  | GLV Battery |  |  |  |  | TRUE | OK
 |  | HV DC/DC converter GLV connection (if applicable) |  |  |  |  | TRUE | OK
T.9.2.2 |  | GLV Fuse |  |  |  |  | TRUE | OK
 |  | Wire Gauge |  |  |  |  | TRUE | OK
EV.7.1.2 |  | Precharge Contactor coil |  |  |  |  | TRUE | OK
EV.7.1.2 |  | Positive AIR coil |  |  |  |  | TRUE | OK
EV.7.1.2 |  | Negative AIR coil |  |  |  |  | TRUE | OK
EV.5.6.3a |  | Discharge Contactor coil |  |  |  |  | TRUE | OK
EV.7.9.1; EV.7.9.3 |  | TSMS is last switch |  |  |  |  | TRUE | OK
EV.7.9.1; EV.7.9.2 |  | GLVMS is first switch |  |  |  |  | TRUE | OK
 |  | Uses proper electrical schematic symbols |  |  |  |  | TRUE | OK
 |  | Labels/text are readable (zooming in is acceptable) |  |  |  |  | TRUE | OK
EV.5.10 |  | Interlocks on TS connectors outside of an enclosure |  |  |  |  | TRUE | OK
Additional Comments |  |  |  |  |  |  | Rules References
 |  |  |  |  |  |  | EV.7.1 EV.7.2
 |  |  |  |  |  |  |  |  |  | TSAL Schematic Shows |  | OK
 |  |  |  |  |  |  |  |  |  | TSAL controlled by >60V present in TS | TRUE | OK
 |  |  |  |  |  |  |  |  |  | TSAL powered by GLV | TRUE | OK
 |  |  |  |  |  |  |  |  |  | TSAL flashes red when HV present and solid green when not | TRUE | OK
 |  |  |  |  |  |  |  |  |  | Additional Comments | Rules References
 |  |  |  |  |  |  |  |  |  |  | EV.5.9

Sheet: Torque Security
Status | OK
APPS Sensor Transfer function |  |  |  | OK | Torque Control Path Security Checks |  |  |  |  |  |  |  |  | OK
Rules Reference |  | T.4.2.3
Position | APPS1 Output [V] |  | APPS2 Output [V] |  | Source Device | Destination Device | Communication | Redundant | Out Of Range | Correlation | Checksum | Timeout | Other |  | Additional Comments
0% | 1.91 |  | 1.1 | OK
20% | 2.48 |  | 1.67 | #NAME? | APPS | ECU | Analog | 2 sensors | Yes | Yes | No | No |  | OK
40% | 3.00 |  | 2.19 | #NAME? | ECU | Inverter | Digital | No | Yes | No | CAN CRC | 500ms |  | OK
60% | 3.49 |  | 2.68 | #NAME? | Inverter
80% | 4.00 |  | 3.19 | #NAME?
100% | 4.5 |  | 3.69 | #NAME?

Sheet: Other
Status | OK
Motor Controller |  |  |  | OK | Motor |  |  | OK
Make |  | Rinehart Motion Systems LLC |  | OK | Make |  | Emrax | OK
Model |  | PM100DX |  | OK | Model |  | 228 HV CC | OK
Datasheet |  | PM100DX |  | OK | Datasheet |  | Emrax 228 | OK
Galvanic Isolation between TS and control |  | 1000 | V | OK
Picture of Energy Meter download connector on car to prove compliance with EV.3.2.2
Energy Meter Download Picture Shows |  |  |  |  |  | OK
Energy Meter Download Connector |  |  |  |  | TRUE | OK
Additional Comments
The master switch will be approximately located where the cutout on the LV shutdown panel is. The absolute location is unkown but will not move from the panel shown.

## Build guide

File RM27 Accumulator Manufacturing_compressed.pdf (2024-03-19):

## RM27 Accumulator Manufacturing 2024

Author: Sean Trimper - EV Lead/ESO (603)204-0353 - strimper13@gmail.com

Manufacturing Timeline:
- Accumulator One RTD (4/15/24)
- System level testing
- Insulation installed
- Wiring complete (GLV & TS)
- Components in accumulator (3/25/24)
- Segments ready for install (3/11/24)
- BMS voltage taps connected
- Segments spot-welded (2/12/24)
- Material list by (1/15)
- BMS thermistors installed
- MT Plugs installed
- Precharge installed + wired
- Discharge installed + wired
- IMD installed + wired
- Accu Indicator installed + wired
- TSAL installed + wired
- AIRs installed + wired to main fuse
- Main fuse installed + wired to AIRs and MT Plugs
- External plugs installed + wired to AIRs
- HVD installed + wired to external plugs
- Energy meter installed + wired
- Charging (4/1/24)
- Shutdown circuit integration
- Wall outlet integration
- Accumulator two (4/29/24)
- Parallel

Cell Prep:
- Prior to spot welding
- Inspect cells for physical damage
- Measure cell and ensure it is in voltage range of 3.5-3.7V

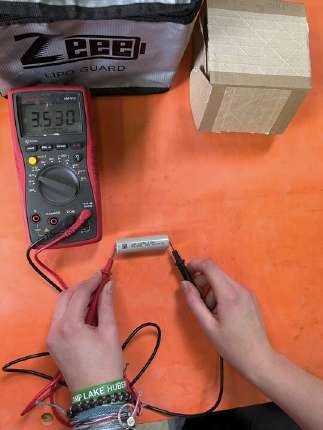
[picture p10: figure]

- If any cells are not good (damage or out of voltage range): set aside, note issue, and tell ESO
- Label boxes of measured and inspected cells with: name & date measured
- Stick insulative rings on positive terminals of each cell

Segment Manufacturing:

Making the segment skeletons (segment without any cells)
- Waterjet cell holders
- Assemble cell holder (two sheets (+ & -) using hex nylon standoff and specific bolts)
- Ensure that the - and + sheets are on the correct side when assembled (verify with CAD)
- If bolts are misplaced, check the McMaster order to verify which bolts are needed

Setting up the segment and welder
- Place a thin nonconductive sheet under the segment being welded. This allows the inserted cells to rest at the correct height (if no sheet was there, the cells would be too low due to the standoff bolts)
- Turn on the power supply connected to the spot welder
- It will do some checks, turn on the fans, then start clicking as the capacitors charge. This is normal.
- When done, turn off power supply, unplug from wall, and set welder to 0.0J

Nickel busbars
- Insert cells sticker side down across the segment (6 cells)
- Try to align all cell wrapper labels the same direction

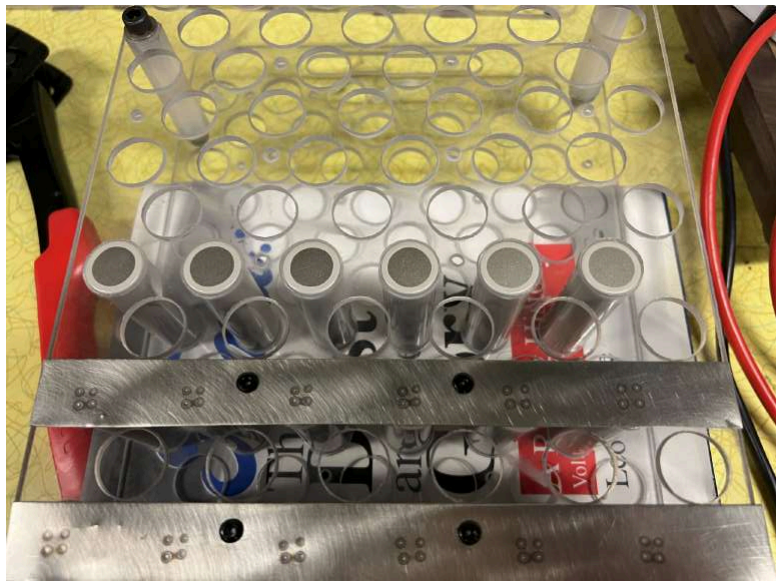
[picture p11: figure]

- Place nickel busbar overtop the cells
- Ensure that the bus bars do not extend past the polycarb. If they do, trim them lightly with tin snips and sand to get a smooth edge (aim for within 1mm to edge of polycarb)
- Insert rivets into holes of nickel strips on one side (2 holes)

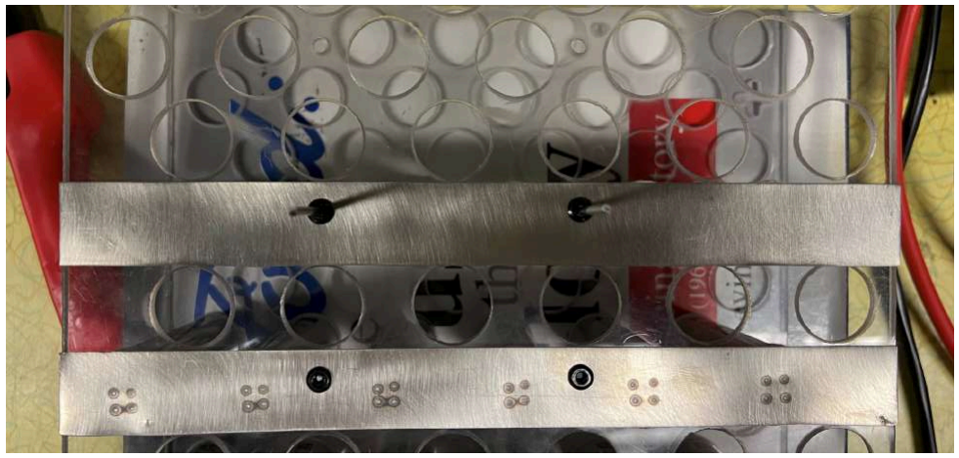
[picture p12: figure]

- Spot weld negative ends with nickel bus bars (2 welds per cell), 75.1J setting
- Line up busbar in between the cells on either side of it (sticker side cells, next row over)
- Apply decent pressure downwards with probes
- If a bad weld occurs (welder will make an different beeping noise), do an additional weld (3 total)

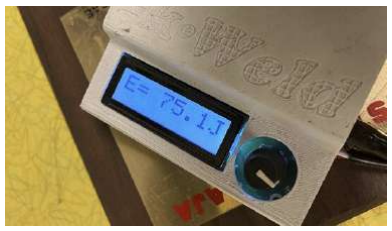
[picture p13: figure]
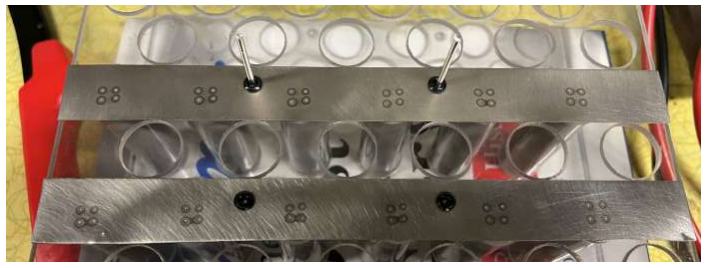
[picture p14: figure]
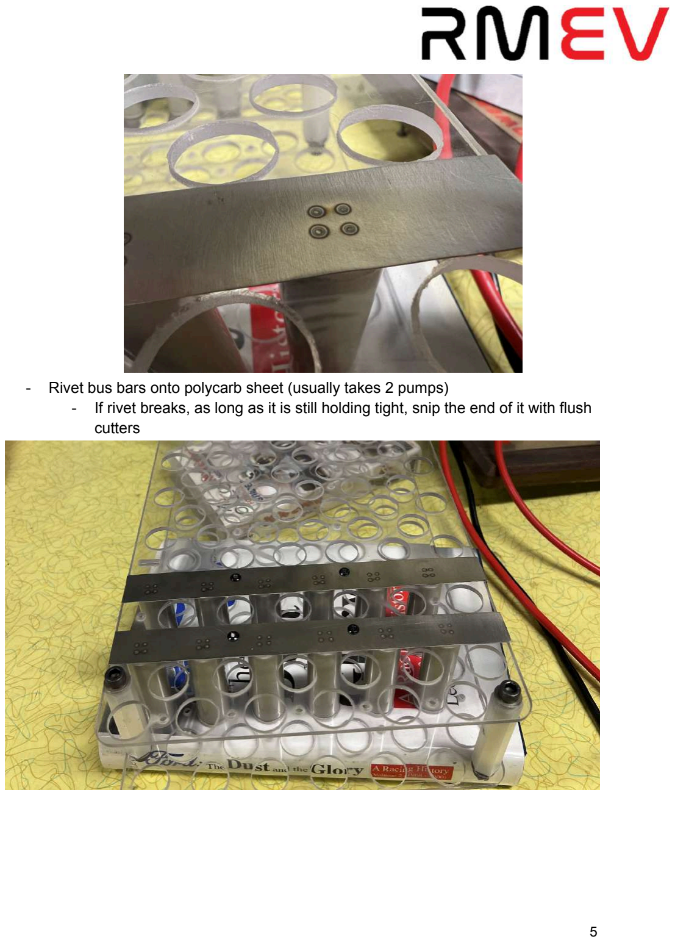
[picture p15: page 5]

- Rivet bus bars onto polycarb sheet (usually takes 2 pumps)
- If rivet breaks, as long as it is still holding tight, snip the end of it with flush cutters

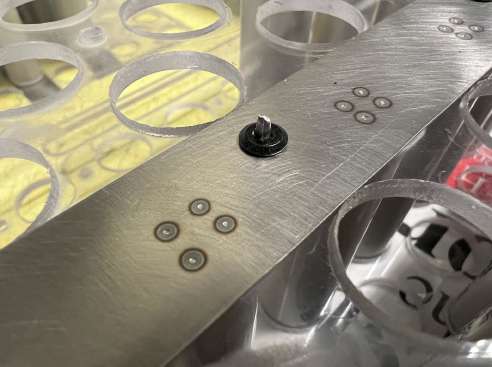
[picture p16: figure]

- Continue this process until all negative bus bars are welded on side 1
- Flip over and do the same on the other side of the segment

Copper collectors
- Negative pole
- Insert rivets into copper bus bar slots through nickel strip
- Spot weld nickel strip onto negative sides of cells
- Remove rivets, insert through copper and nickel bus bar, and rivet copper and nickel to cell holder
- Positive pole
- Insert rivets into copper bus bar slots through nickel strip
- Spot weld nickel strip onto POSITIVE side of cells
- Remove rivets, insert through copper and nickel bus bars, and rivet copper and nickel to cell holder

You should now have all negative connections made, copper bus bars placed onto negative AND positive sides of the segment, and all of those riveted and spot welded down

- Scary fuse things next!

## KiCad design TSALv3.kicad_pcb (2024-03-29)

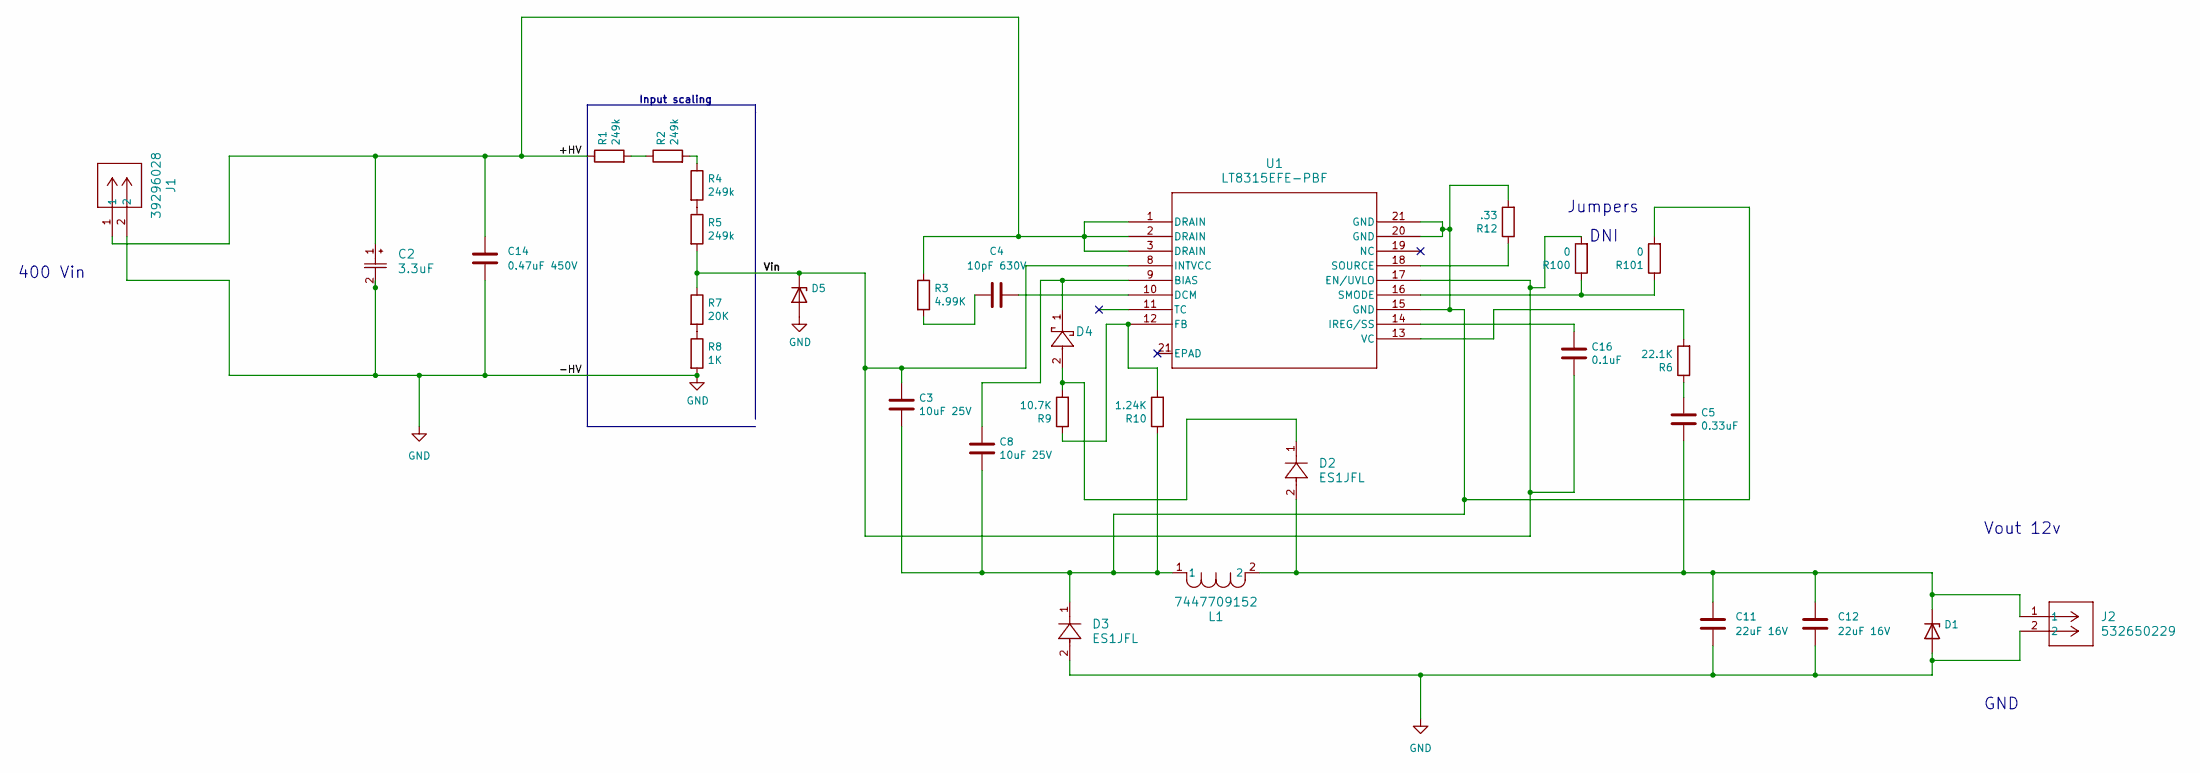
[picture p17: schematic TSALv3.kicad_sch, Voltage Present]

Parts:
C2: 3.3uF; CAP_ULH_8X10_NCH
C3: 10uF 25V; C_0603_1608Metric_Pad1.08x0.95mm_HandSolder
C4: 10pF 630V; C_1206_3216Metric
C5: 0.33uF; C_0603_1608Metric_Pad1.08x0.95mm_HandSolder
C8: 10uF 25V; C_1206_3216Metric_Pad1.33x1.80mm_HandSolder
C11, C12: 22uF 16V; C_1210_3225Metric_Pad1.33x2.70mm_HandSolder
C14: 0.47uF 450V; C_1812_4532Metric
C16: 0.1uF; C_0603_1608Metric_Pad1.08x0.95mm_HandSolder
D1, D5: D_SMB
D2, D3: ES1JFL; SOD-123FL_425AD_OSI
D4: CMDSH2-3 TR PBFREE; SDO_CMDSH2-3 TR PBFREE_CNS
J1: 39296028; CON_39296028
J2: 532650229; CON_532650229_MOL
L1: 7447709152; IND_1210-WE-PD_WRE
R1, R2, R4, R5: 249k; RC1210N_VIS
R3: 4.99K; R_1206_3216Metric
R6: 22.1K; R_0603_1608Metric_Pad0.98x0.95mm_HandSolder
R7: 20K; RC1210N_VIS
R8: 1K; RC1210N_VIS
R9: 10.7K; R_0201_0603Metric_Pad0.64x0.40mm_HandSolder
R10: 1.24K; R_0603_1608Metric_Pad0.98x0.95mm_HandSolder
R12: .33; R_0603_1608Metric
R100, R101: 0; R_0603_1608Metric
U1: LT8315EFE-PBF; FE_20_ADI-L

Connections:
/+HV: C2.1, C14.1, J1.1, R1.1, R3.1, U1.1 (DRAIN), U1.2 (DRAIN), U1.3 (DRAIN)
/Vin: C3.1, C16.2, D5.1 (K), R5.2, R7.1, R100.2, U1.8 (INTVCC), U1.17 (EN/UVLO)
GND: C2.2, C11.2, C12.2, C14.2, D1.2 (A), D3.2, D5.2 (A), J1.2, J2.2, R8.2
unnamed: C3.2, C8.2, D3.1, L1.1, R10.1, R12.2, R101.2, U1.15 (GND), U1.20 (GND), U1.21 (GND)
unnamed: C4.2, R3.2
unnamed: C5.1, R6.1
unnamed: C5.2, C11.1, C12.1, D1.1 (K), D2.2, J2.1, L1.2
unnamed: D2.1, D4.2, R9.2
unnamed: R1.2, R2.1
unnamed: R2.2, R4.1
unnamed: R4.2, R5.1
unnamed: R7.2, R8.1
unnamed: C8.1, D4.1, U1.9 (BIAS)
unnamed: C4.1, U1.10 (DCM)
unnamed: R9.1, R10.2, U1.12 (FB)
unnamed: C16.1, U1.14 (IREG/SS)
unnamed: R100.1, R101.1, U1.16 (SMODE)
unnamed: R12.1, U1.18 (SOURCE)
unnamed: R6.2, U1.13 (VC)

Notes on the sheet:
Input scaling
DNI
Vout 12v
Jumpers
400 Vin
GND

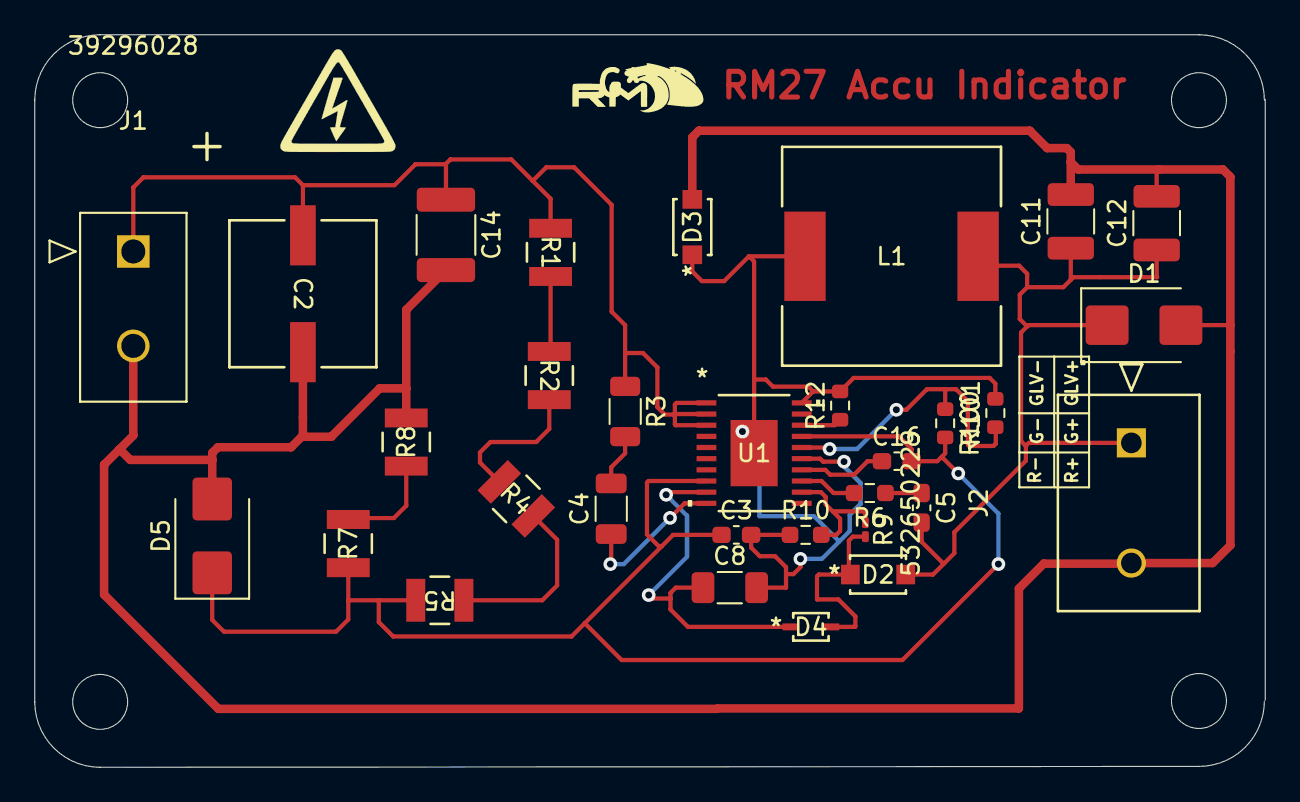
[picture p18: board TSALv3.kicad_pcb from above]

Board: 2 copper layers, 71.7 x 42.7 mm, 35 parts (0 on the bottom side), 19 nets.

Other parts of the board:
MH1, MH2, MH3, MH4: MountingHole_3.2mm_M3

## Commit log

2024-01-30 WIP TSAL
    Adding WIP TSAL which has TSAL and voltage indicator. Transformer is messed up
2024-02-06 RM27 ESF 2.0
    Added better resolution pictures, updated TSAL schematic, and updated HV component locations
2024-02-06 Swap 12V comparators LT1441 with LM393
2024-02-09 Increase comparator terminal resistances to increase stability
2024-02-09 TSAL BOM
    Bill of materials for RM27 TSAL circuit
    [RM27 TSAL BOM(1).xlsx]
2024-02-16 Edit diode types and placement
2024-02-23 ESF V3
    Third version of RM27 ESF. Updated schematics, datatsheets, and pictures + CAD
2024-02-23 RM27 Accumulator Tractive System Schematic
    Updated TS schematic showing all connectors, updated hardware locations, and additional circuitry such as fuses for the IMD.
    [RM27_Accu_TS_Schematic.kicad_sch]
2024-02-23 Use easily available (LT1011) comparators, fix some annotations on schematic
2024-02-27 RM27 Charging Shutdown Circuit
    Updated charging shutdown circuit to reflect design changes in accumulator.
2024-03-01 Fix minor wiring errors in 555 timer
2024-03-01 Decrease output resistance so LED can activate
2024-03-01 BOM for Mercer Demo Board
    All part numbers, links, etc.
    [Mercer Demo Board BOM(1).xlsx]
2024-03-12 RM27 Accumulator Manufacturing Doc
    Shows how to assemble the accumulator segments. For reference only with pictures.
2024-03-12 Generate BMS Wiring Diagram
    This was generated on https://www.orionbms.com/tools/wiring.php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.
    There are 19 cells in each row of the accumulator, so halfway through the middle group, the cells are all tied to the cell that is a multiple of 19. In the left group, they are all listed as N/A beca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
2024-03-15 Accumulator Indicator Initial Schematic
    initial draft. turns on if TS voltage is greater than 60V. Runs completely off of accumulator voltage and is attached to the AIRs.
    [AccuIndicator.kicad_sch]
2024-03-15 TSAL mating connectors (LV + HV)
    Picture showing mating connectors for TSAL board. These are the connectors which go on the GLV and HV wiring harnesses to plug into the TSAL board. Parts are available on Digikey
2024-03-19 Indicator Light
    Revised layout of indicator light. Vias added
    [TSALv3.kicad_pcb]
2024-03-29 Accu Indicator V3
    Added logo, final design changes. Pending HV/LV Spacing
    [TSALv3.kicad_pcb, TSALv3.kicad_sch]
2024-03-29 RM KiCad Logo
    Logo for KiCad PCB files
2024-04-05 Redraw the Demo Board Schematic so it's more readable
2024-04-05 Accumulator Indicator V1 Gerber Files
    Gerber and drill files to print PCB for accumulator indicator
2024-04-05 Add spec sheet with input/output limits and performance info for CAN bus charger
2024-04-05 RM27 TSAL Gerbers
    Drill and Gerber files for RM27 final TSAL
2024-04-11 Updated new maintenance plugs for mr trimper
    [RM27_Accu_TS_Schematic.kicad_sch]
2024-04-12 Accumulator Indicator with new silkscreen
    Updated silkscreen to have proper labeling and got rid of residual labels
2024-04-12 Update README.md with description of soldering board
2024-04-12 Accumulator Indicator BOM
    BOM with part #s and # of parts for accumulator indicator
    [New Design Parts List 4-1-24.xls]
2024-04-12 Clean up schematic (V2) and add accurate component labels
2024-04-16 RM27 ESF V4
    Final iteration of RM27 ESF
    [RM27 ESF V4.0.xlsx]
